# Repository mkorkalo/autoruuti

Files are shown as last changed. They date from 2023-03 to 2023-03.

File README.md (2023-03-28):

# autoruuti
Automatic gunpowder dispenser for ammunition reloading use.

Don't want to spend 1500 USD for a precision automatic powder dispenser? Build your own.
Cost for the electronics is less than 50 €, plus a laboratory scale worth about 290 €.

See [my youtube video](https://www.youtube.com/watch?v=Eo732I7xDfE&t=23s) for a short demo.

## Required hardware
These are what I used. I am not affiliated with any of these manufacturers or shops.

* [Laboratory scale KERN EMB-V 200-3V](https://vaakaekspertti.fi/laboratoratoriovaaka-kern-emb-v.html). I believe any KERN scale with RS-232 port should work, but verify that it supports the [KERN KCP protocol](https://dok.kern-sohn.com/manuals/files/English/KCP-ZB-e-v1.3.7.pdf).
* [TTL-RS232 converter](https://www.aliexpress.com/item/1005003091082827.html)
* [Arduino Uno R3 (clone)](https://www.aliexpress.com/item/1005003363526075.html)
* [LCD keypad shield (clone)](https://www.aliexpress.com/item/1005004889066625.html)
* [28BYJ-48-5V 4 phase stepper motor + ULN2003 controller board](https://www.aliexpress.com/item/1005004566735226.html)
* [Frankford Arsenal powder dispenser](https://www.metsovaruste.fi/metsastysmaailma/ruutisirotin-frankford-arsenal/p/60-025-3985/). You can use any other powder dispenser, but the included 3D model for the mechanical adapter & holder will probably not fit and adjustments will be needed.
* A 5 volt power supply directly connected to the 5V rail of the Uno board. Do not use the included 12V to 5V DC converter, it will not supply enough power for the stepper motor and you will have problems.
* A male to male RS-232 serial cable. I made my own cable from DB9 male connectors. Only TXD, RXD & GND are required (and rx/tx needs to be cross connected of course).
* A 3D printer capable of printing at least PLA. I used PETG but PLA and others should work just fine. Almost any printer will do.

## Electronic assembly

* Place LCD keypad shield on top of the arduino uno board.
* Connect 5V rail directly to the 5V rail of Uno and GND to Uno GND.
* Also connect power supply 5V & GND directly to the ULN2003 controller board.
* Connect 5V & GND to ULN2003 5V & GND.
* Connect IN1, IN2, IN3, IN4 of ULN2003 to Uno pins A5, A4, A3 and A2.
* Connect serial converter RX to D3 and TX to D2
* Recommended: USB-A male connector for supplying power to the unit. I use a USB-A male connector to power the device and I've found it works best for me. I can even power the device using a power bank.

See [Arduino UNO pinout diagram](https://images.prismic.io/circuito/8e3a980f0f964cc539b4cbbba2654bb660db6f52_arduino-uno-pinout-diagram.png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,format).

## Mechanical assembly ##

### Main case ###
* I used an [Arduino case I found from thingiverse](https://www.thingiverse.com/thing:3362327) and cut off a piece to make the display assembly fit. Print and install with screws.
* ULN2003 board can fit inside but needs an enclosure of some thing, I just used electrical tape.
* I cut off a bit to fit the TTL converter to the side.
* Better enclosure would be nice but I didn't have time to CAD model it yet. Please, share your model if you draw one.

### Powder dispenser ###
* Print cadfiles/dispenser_axle_adapter: 
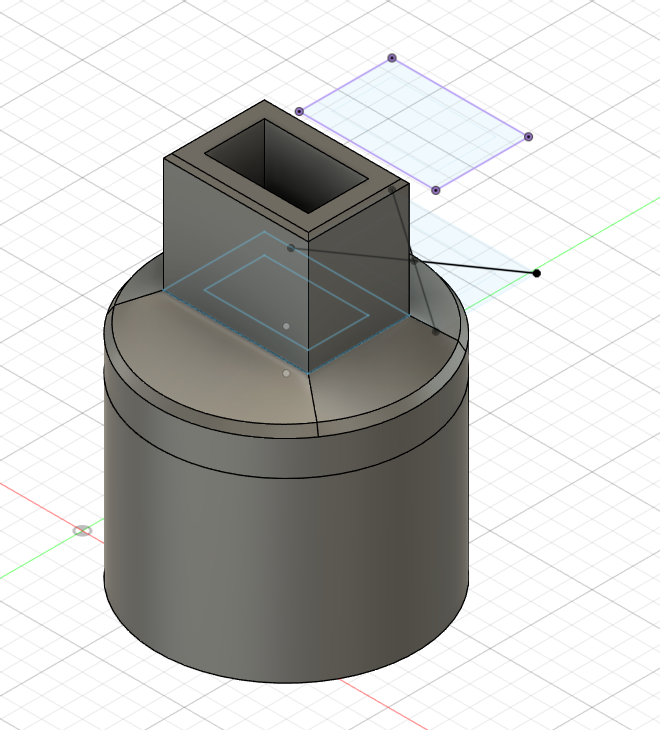
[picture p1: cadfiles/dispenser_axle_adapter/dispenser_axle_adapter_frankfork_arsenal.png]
Dispenser axle adapter


* Print cadfiles/motor_mount
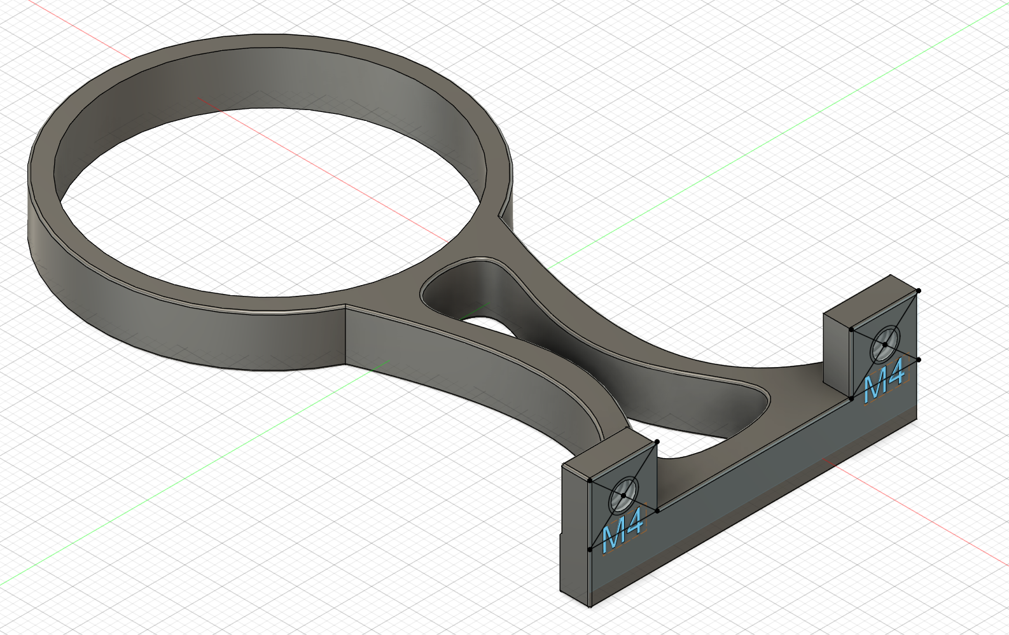
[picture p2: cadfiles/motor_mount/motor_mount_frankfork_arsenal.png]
Motor mount

* Assemble the model as seen in the youtube video. It's a tight fit but worked for me.

## Software

* Install [Arduino IDE] (https://www.arduino.cc/en/software)
* Install a few arduino libraries:
   * [Regexp by Nick Gammon](https://github.com/nickgammon/Regexp)
   * [LCDKeypad by dzindra](https://github.com/dzindra/LCDKeypad)
* Other built-in libraries used: Stepper, SoftwareSerial, EEPROM. These do not require any 3rd party downloads.

* Flash autoruuti.ino with Arduino IDE using the included USB-A - USB-B cable.
* You should see startup texts when powering the device. If not, then your display is not properly connected.

## Usage

* Menu/UI is in finnish. Contact me if you wish to use it but don't speak finnish, I can provide a translation :)
* Default values will be loaded on first boot.
* Hold the SELECT button to enter menu.
* Short press the SELECT button to enter/leave pause mode.
* Use LEFT/RIGHT keys to navigate the menu.
* Use UP/DOWN keys to change the setting: short press for a small change and long press for a large change.
* Settings are saved automatically within 5 seconds of modification. Changing the settings often will not burn out your EEPROM.
* Rightmost button is reset and will perform a hardware reset (EEPROM settings will not be lost)
* Adjust speeds to match your powder and stepper/board combination.

### Notes on accuracy of the KERN EMB-V 200

* Always ZERO your scale between cases! As the [KERN EMB-V manual](https://dok.kern-sohn.com/manuals/files/English/EMB-V-BA-e-1624.pdf) mentions, it is not accurate for dynamic add-on weighing procedures:
> Do not use balance for dynamic add-on weighing procedures, if
> small amounts of goods to be weighed are removed or added.
> The “stability compensation“ installed in the balance may result
> in displaying an incorrect measuring value!
> (Example: Slowly draining fluids from a container on the balance.)

Technically, using the scale for powder measurement is Improver use as per the definition in manual, however I have found out that the accuracy is more than enough if you don't keep adding/removing powder for a long time and zero between measurements.
You can achieve maybe about +/- 2 mg of accuracy with correct use and settings.

# License

[CC BY-NC-SA 4.0](https://creativecommons.org/licenses/by-nc-sa/4.0/)

Not for commercial use. Please contact me if you wish to sell these.
If you think some other license would work better, let me know.

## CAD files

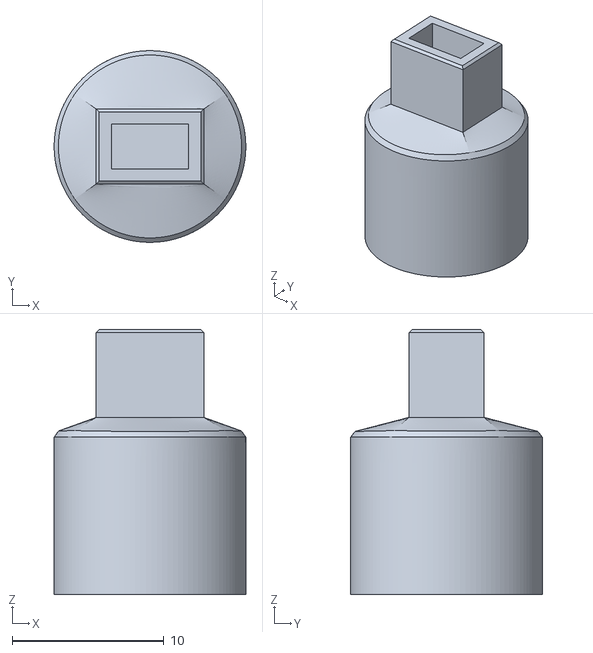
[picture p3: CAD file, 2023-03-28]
cadfiles/dispenser_axle_adapter/dispenser_axle_adapter_frankfork_arsenal.stl
12.6 x 12.6 x 17.5

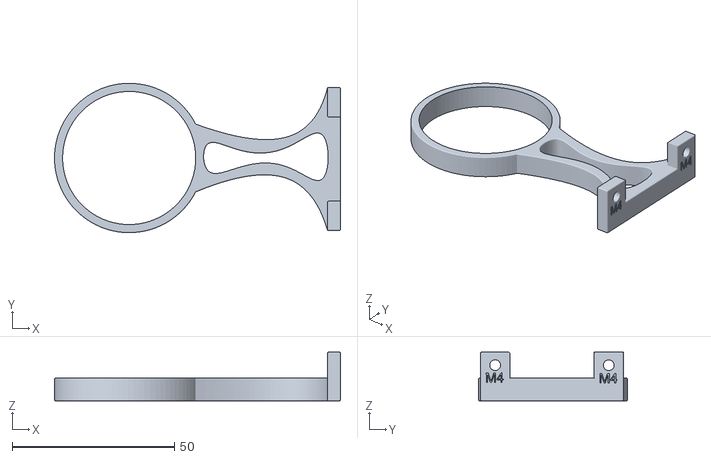
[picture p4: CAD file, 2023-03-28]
cadfiles/motor_mount/motor_mount_frankfork_arsenal.stl
88.1 x 46.0 x 15.0

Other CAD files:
cadfiles/dispenser_axle_adapter/dispenser_axle_adapter_frankfork_arsenal.f3z
cadfiles/motor_mount/motor_mount_frankfork_arsenal.f3d

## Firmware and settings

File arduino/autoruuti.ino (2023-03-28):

#include <LiquidCrystal.h>
#include <LCDKeypad.h>
#include <SoftwareSerial.h>
#include <Stepper.h>
#include <Regexp.h>
#include <EEPROM.h>

//RX: D3
//TX: D2
SoftwareSerial scale(3, 2);

LCDKeypad lcd;

int incomingByte = 0; // for incoming serial data

const int INPUT_BUFFER_SIZE = 64;
char inputBuffer[INPUT_BUFFER_SIZE];

// Defines the number of steps per rotation
const int measureTimeout = 15;

MatchState ms;

const int SCALE_ERROR_TIMEOUT = -1001;
const int SCALE_ERROR_REPLY_FORMAT = -1000;

const int LONG_BUTTON_PRESS_MS = 800;
unsigned long lastButtonDownEventMs = 0;  //in millis(). if > 0, a button down event was occured.
uint8_t lastButtonDownType;               //KEYPAD_DOWN, KEYPAD_UP etc
bool lastButtonLongPressEmitted = false;  //This is for tracking if the long press event was already emitted (so we don't do it again)
const int timerValue = 0;

const int SETTINGS_HEADER1_I = 0;
const int SETTINGS_HEADER1_V = 0xF0;
const int SETTINGS_HEADER2_I = 1;
const int SETTINGS_HEADER2_V = 0x01;
const int SETTINGS_VERSION_I = 2;
const int SETTINGS_VERSION_V = 1;
const int SETTINGS_STRUCT_I = 3;
const int STEPS_PER_ROTATION = 2038;

// Pins entered in sequence IN1-IN3-IN2-IN4 for proper step sequence
Stepper stepper(STEPS_PER_ROTATION, A5, A4, A3, A2);

uint8_t mode = 0;   //0 = operation, 1 = settings menu
#define MODE_OPERATION 0
#define MODE_SETTINGS 1

bool paused = true;
bool saveRequired = false;

#define PHASE_WAIT 0
#define PHASE_1 1
#define PHASE_2 2
#define PHASE_3 3
#define PHASE_COMPLETE 4
#define PHASE_OVERWEIGHT 5

uint8_t phase = 0;        //what phase are we in (1-3), 0=waiting startWeight, 4=complete, 5=overweight
double weight = 0.0;  //last measured weight
bool weightError = true;

#define MENUITEM_COUNT 12
uint8_t menuitem = 0;
#define MENUITEM_STARTWEIGHT 0
#define MENUITEM_TARGETWEIGHT 1
#define MENUITEM_PHASE1SPEED 2
#define MENUITEM_PHASE2SPEED 3
#define MENUITEM_PHASE3SPEED 4
#define MENUITEM_STABILIZETIMEMS 5
#define MENUITEM_PHASE1WEIGHT 6
#define MENUITEM_PHASE2WEIGHT 7
#define MENUITEM_OVERWEIGHTWARNING 8
#define MENUITEM_PHASE1ROTATIONS 9
#define MENUITEM_PHASE2ROTATIONS 10
#define MENUITEM_PHASE3ROTATIONS 11
const char *menuitem_names[] = {
  "Aloituspaino g",
  "Tavoitepaino g",
  "Vaihe 1 nopeus ask",
  "Vaihe 2 nopeus ask",
  "Vaihe 3 nopeus ask",
  "Stabilointiaika ms",
  "Vaihe 1 painoero g",
  "Vaihe 2 painoero g",
  "Ylipainovaroitus g",
  "Vaihe 1 kierrokset",
  "Vaihe 2 kierrokset",
  "Vaihe 3 kierrokset"
};
const double menuitem_modifiers_short[] = {
  0.1,
  0.001,
  1.0,
  1.0,
  1.0,
  100.0,
  0.01,
  0.002,
  0.001,
  0.05,
  0.05,
  0.05
};
const double menuitem_modifiers_long[] = {
  1.0,
  0.1,
  5.0,
  5.0,
  5.0,
  500.0,
  0.1,
  0.1,
  0.01,
  0.5,
  0.5,
  0.5
};

unsigned long settingsChangedTimeMs = 0;


// STORED SETTINGS
struct settings_t {
  double startWeight;             //e.g. 2.5    when to start addition
  double targetWeight;            //e.g. 3.3    how much we want the weight to be
  int phase1Speed; //50           //e.g. 50     phase 1 addition speed
  int phase2Speed; //20           //e.g. 20     phase 2 addition speed
  int phase3Speed; //5            //e.g. 5      phase 3 addition speed
  int stabilizeTimeMs;            //e.g. 5000   scale stabilization time in ms
  double phase1Weight;            //e.g. 0.1    when we're missing this much weight, go to phase 2
  double phase2Weight;            //e.g. 0.05   when we're missing this much weight, go to phase 3
  double overWeightWarning;       //e.g. 0.02   if we go this much over target, display a warning
  double phase1Rotations;         //e.g. 0.5
  double phase2Rotations;         //e.g. 0.25
  double phase3Rotations;         //e.g. 0.05   when doing phase 3 measurement, how much to add at once (rotations)
};

struct settings_t settings;

void loadDefaults() {
  Serial.println("load hardcoded default settings");

  //load default settings
  memset(&settings, 0, sizeof(settings_t));
  settings.startWeight = 2.0;
  settings.targetWeight = 3.3;
  settings.phase1Speed = 10;
  settings.phase2Speed = 10;
  settings.phase3Speed = 10;
  settings.stabilizeTimeMs = 5000;
  settings.phase1Weight = 0.1;
  settings.phase2Weight = 0.05;
  settings.overWeightWarning = 0.01;
  settings.phase1Rotations = 0.5;
  settings.phase2Rotations = 0.25;
  settings.phase3Rotations = 0.05;
}

void loadSettings() {
  Serial.println("load settings from EEPROM");

  //load settings from EEPROM, or if all fails, load default settings
  //#0, #1: expect static header, 0xF001
  uint8_t header1 = EEPROM.read(SETTINGS_HEADER1_I);
  uint8_t header2 = EEPROM.read(SETTINGS_HEADER2_I);
  if (header1 != SETTINGS_HEADER1_V || header2 != SETTINGS_HEADER2_V) {
    Serial.println("Header mismatch, load defaults");
    loadDefaults();
    return;
  }

  //Settings version number. Not really used right now but for future.
  uint8_t version = EEPROM.read(SETTINGS_VERSION_I);
  if (version != SETTINGS_VERSION_V) {
    Serial.println("Version mismatch, load defaults");
    loadDefaults();
    return;
  }

  //looks good, load defaults
  Serial.println("Load settings");

  EEPROM.get(SETTINGS_STRUCT_I, settings);
}

void saveSettings() {
  Serial.println("save settings to EEPROM");
  EEPROM.write(SETTINGS_HEADER1_I, SETTINGS_HEADER1_V);
  EEPROM.write(SETTINGS_HEADER2_I, SETTINGS_HEADER2_V);
  EEPROM.write(SETTINGS_VERSION_I, SETTINGS_VERSION_V);
  EEPROM.put(SETTINGS_STRUCT_I, settings);

  settingsChangedTimeMs = 0;
}

void settingsChanged() {
  settingsChangedTimeMs = millis();
}

void print_error(String error1, String error2)
{
  lcd.clear();
  lcd.setCursor(0, 0);
  lcd.print(error1);
  lcd.setCursor(0, 1);
  lcd.print(error2);
  delay(5000);
}

int readScaleMeasurement()
{
  memset(inputBuffer, 0, INPUT_BUFFER_SIZE);
  int read = scale.readBytesUntil('\n', inputBuffer, INPUT_BUFFER_SIZE - 1);
  //Serial.print("read ");
  //Serial.print(read);
  //Serial.print("\r\n");
  //for (int k=0; k<read; k++) {
  //  Serial.print(int(inputBuffer[k]));
  //}
  //Serial.print(inputBuffer);
  //Serial.print("\r\n");

  if (read == 0) {
    weightError = true;
    return SCALE_ERROR_TIMEOUT;
  }
  for (int k=0; k<read; k++) {
    if (inputBuffer[k] == '\r' || inputBuffer[k] == '\n') {
      inputBuffer[k] = 0;
    }
  }
  ms.Target(inputBuffer);
  char match = ms.Match("%s*(-*%s*%d+.%d+) g", 0);
  if (match != REGEXP_MATCHED) {
    //print_error("ERROR in reply:", inputBuffer);
    weightError = true;
    return SCALE_ERROR_REPLY_FORMAT;
  }

  //Unsafe code. GetCapture does not support max len?
  char parsedValue[50];
  ms.GetCapture(parsedValue, 0);
  String str(parsedValue);
  str.replace(" ", "");
  //Serial.print("str ");
  //Serial.print(str);
  //Serial.print("\r\n");

  double value = atof(str.c_str());
  Serial.print("Read weight: ");
  Serial.print(value, 3);
  Serial.print("\r\n");
  weight = value;
  weightError = false;
  return 0;
}

int measure(bool stable)
{
  for (int k=0; k<measureTimeout; k++) {
    //discard all data
    scale.readBytes(inputBuffer, INPUT_BUFFER_SIZE);
    lcd.setCursor(15, 1);
    lcd.print("P");

    if (stable)  {
      scale.write("S\r\n");
      //Serial.print("write S\r\n");
    } else {
      //scale does not support SI? protocol looks different from the PDF...
      scale.write("SI\r\n");
      //Serial.print("write SI\r\n");
    }
    int ret = readScaleMeasurement();
    if (ret == SCALE_ERROR_TIMEOUT) {
      delay(500);
      continue;
    } else if (ret == SCALE_ERROR_REPLY_FORMAT) {
      delay(500);
      continue;
    }
    lcd.setCursor(15, 1);
    lcd.print(" ");
    return 0;
  }
  lcd.setCursor(15, 1);
  lcd.print("E");
  return SCALE_ERROR_TIMEOUT;
}

void pause() {
  paused = true;
}

void unpause() {
  paused = false;
}

void determinePhase(bool recursive) {
  bool stableRead = true;
  if (phase == PHASE_1) {
    stableRead = false;
  }
  double beforeWeight = weight;
  int ret = measure(stableRead);
  if (ret) {
    return;
  }

  int lastPhase = phase;

  // phase 1
  if (weight > (settings.targetWeight + settings.overWeightWarning)) {
    pause();
    phase = PHASE_OVERWEIGHT;
  } else if (weight >= (settings.targetWeight - 0.001)) {
    phase = PHASE_COMPLETE;
  } else if (weight > settings.targetWeight - settings.phase2Weight) {
    phase = PHASE_3;
  } else if (weight > settings.targetWeight - settings.phase1Weight) {
    phase = PHASE_2;
  } else if (weight > settings.startWeight) {
    phase = PHASE_1;
  } else {
    phase = PHASE_WAIT;
  }

  if (!stableRead && phase != PHASE_1) {
    if (recursive) {
      //weight changed again, give up and retry later
      return;
    }
    //phase was changed from 1, run againt to do a stable reading
    determinePhase(true);
  }

  if (beforeWeight != weight || lastPhase != phase) {
    drawOperationStatus();
  }
}

void runPhase(
  ) {
  //Addition will be done only if:
  // * Measured (stabilized) weight >= minWeight and <maxWeight
  
  //Phase 1
  //- add using phase 1 speed until we measure targetWeight - phase1Weight (fast read)
  //- start phase 2
  //Phase 2
  // - add using phase 2 speed until we measure targetWeight - phase2Weight (fast read)
  // - start phase 3
  //Phase 3
  // - add using phase 3 rotations
  // - stabilize
  // - read stabilized weight
  // - if less than target, do again

  Serial.print("runPhase w=");
  Serial.print(weight, 3);
  Serial.print(" phase=");
  Serial.print(phase);
  Serial.println("");

  if (phase == 1) {
    performAddition(settings.startWeight, settings.phase1Speed, settings.targetWeight - settings.phase1Weight, settings.phase1Rotations, false, 0, settings.targetWeight + settings.overWeightWarning);
  } else if (phase == 2) {
    performAddition(settings.startWeight, settings.phase2Speed, settings.targetWeight - settings.phase2Weight, settings.phase2Rotations, false, 0, settings.targetWeight + settings.overWeightWarning);
  } else if (phase == 3) {
    performAddition(settings.startWeight, settings.phase2Speed, settings.targetWeight, settings.phase3Rotations, true, settings.stabilizeTimeMs, settings.targetWeight + settings.overWeightWarning);
  }
}

void printWeight(double weight, bool stable, double target)
{
  lcd.setCursor(0, 1);
  lcd.print(weight, 3);
  lcd.print(" / ");
  lcd.print(target, 3);
  lcd.print(" g");
  lcd.print("        ");
}

void printPhase(int phase, double phaseTarget, double finalTarget) {
  lcd.setCursor(0, 0);
  lcd.print("Target ");
  lcd.print(finalTarget);
  lcd.print(" Pha");
  lcd.print(phase);
  lcd.print("      ");
}

void performAddition(double startWeight, int speed, double target, double rotations, bool stableMeasure, int stabilizeTimeMs, double overWeightLimit) {
  if (stabilizeTimeMs) {
    delay(stabilizeTimeMs);
    while (measure(false)) {
    }
    draw();
  }
  if (weight < startWeight) {
    return;
  }
  if (weight >= target) {
    return;
  }
  lcd.setCursor(15, 1);
  lcd.print("M");
  stepper.setSpeed(speed);
  stepper.step(rotations * STEPS_PER_ROTATION);
  lcd.setCursor(15, 1);
  lcd.print(" ");
}

void setup() {
  loadSettings();

  lcd.begin(20, 2);
  lcd.clear();
  lcd.backlight();
  lcd.print("Autoruuti v1.0");

  Serial.begin(9600);
  Serial.print("booting\r\n");
  Serial.println("A");
  Serial.println(3.301 > 3.300);
  Serial.println("B");
  Serial.println(3.302 > 3.300);
  Serial.println("C");
  Serial.println(3.308 > 3.300);
  Serial.println("D");
  Serial.println(3.300 >= 3.300);
  Serial.println("E");
  Serial.println(3.301 >= 3.300);
  Serial.println("F");
  Serial.println(3.299 >= 3.300);

  scale.setTimeout(500);
  scale.begin(9600);
  lcd.setCursor(0, 1);
  lcd.print("Moottoritesti...");
  stepper.setSpeed(10);
  stepper.step(STEPS_PER_ROTATION * 0.1);
  delay(500);
  do {
    lcd.setCursor(0, 1);
    lcd.print("Puntaritesti...  ");
    while (measure(true)) {
    }
    delay(1000);
    lcd.clear();
  } while(weight <= -1000);

  //set up a timer for button checking
  noInterrupts();
  TCCR1A = 0;
  TCCR1B = 0;
  TCNT1 = timerValue;         // preload timer
  TCCR1B |= 1<<CS01;          // 8 prescaler
  TIMSK1 |= 1<<TOIE1;         // enable timer overflow interrupt ISR
  interrupts();
  determinePhase(false);
  drawOperationStatus();
}

void enterSettings() {
  mode = MODE_SETTINGS;
  drawMenu();
}

void changeSetting(bool down, bool longPress) {
  double modifier;
  if (longPress) {
    modifier = menuitem_modifiers_long[menuitem];
  } else {
    modifier = menuitem_modifiers_short[menuitem];
  }
  if (down) {
    modifier = -modifier;
  }

  switch (menuitem) {
    case MENUITEM_STARTWEIGHT:
      settings.startWeight += double(modifier);
      break;
    case MENUITEM_TARGETWEIGHT:
      settings.targetWeight += double(modifier);
      break;
    case MENUITEM_PHASE1SPEED:
      settings.phase1Speed += int(modifier);
      break;
    case MENUITEM_PHASE2SPEED:
      settings.phase2Speed += int(modifier);
      break;
    case MENUITEM_PHASE3SPEED:
      settings.phase3Speed += int(modifier);
      break;
    case MENUITEM_STABILIZETIMEMS:
      settings.stabilizeTimeMs += int(modifier);
      break;
    case MENUITEM_PHASE1WEIGHT:
      settings.phase1Weight += double(modifier);
      break;
    case MENUITEM_PHASE2WEIGHT:
      settings.phase2Weight += double(modifier);
      break;
    case MENUITEM_OVERWEIGHTWARNING:
      settings.overWeightWarning += double(modifier);
      break;
    case MENUITEM_PHASE1ROTATIONS:
      settings.phase1Rotations += double(modifier);
      break;
    case MENUITEM_PHASE2ROTATIONS:
      settings.phase2Rotations += double(modifier);
      break;
    case MENUITEM_PHASE3ROTATIONS:
      settings.phase3Rotations += double(modifier);
      break;
  }

  settingsChanged();
}

void handleSettingsButtonEvent(uint8_t button, bool longPress) {
  if (button == KEYPAD_RIGHT) {
    menuitem++;
    if (menuitem >= MENUITEM_COUNT) {
      menuitem = 0;
    }
  } else if (button == KEYPAD_LEFT) {
    if (menuitem == 0) {
      menuitem = MENUITEM_COUNT - 1;
    } else {
      menuitem--;
    }
  } else if (button == KEYPAD_UP) {
    changeSetting(false, longPress);
  } else if (button == KEYPAD_DOWN) {
    changeSetting(true, longPress);
  } else if (button == KEYPAD_SELECT) {
    if (settingsChangedTimeMs) {
      saveSettings();
    }
    mode = MODE_OPERATION;
  }
}

void buttonEvent(uint8_t button, bool longPress)
{
  Serial.print("buttonEvent: ");
  Serial.print(button);
  Serial.print(" long=");
  Serial.print(longPress);
  Serial.print("\r\n");

  if (mode == MODE_SETTINGS) {
    handleSettingsButtonEvent(button, longPress);
    draw();
    return;
  }

  if (button == KEYPAD_SELECT && !longPress) {
    if (paused) {
      unpause();
    } else {
      pause();
    }
  } else if (button == KEYPAD_SELECT && longPress) {
    enterSettings();
    settingsChanged();
  } else if (button == KEYPAD_LEFT) {
    if (longPress) {
      settings.targetWeight -= 0.5;
    } else {
      settings.targetWeight -= 0.001;
    }
    settingsChanged();
  } else if (button == KEYPAD_RIGHT) {
    if (longPress) {
      settings.targetWeight += 0.5;
    } else {
      settings.targetWeight += 0.001;
    }
    settingsChanged();
  } else if (button == KEYPAD_UP) {
    if (longPress) {
      settings.targetWeight += menuitem_modifiers_long[MENUITEM_TARGETWEIGHT];
    } else {
      settings.targetWeight += menuitem_modifiers_short[MENUITEM_TARGETWEIGHT];
    }
    settingsChanged();
  } else if (button == KEYPAD_DOWN) {
    if (longPress) {
      settings.targetWeight -= menuitem_modifiers_long[MENUITEM_TARGETWEIGHT];
    } else {
      settings.targetWeight -= menuitem_modifiers_short[MENUITEM_TARGETWEIGHT];
    }
    settingsChanged();
  }
  draw();
}

void checkButtons() {
  uint8_t button = lcd.buttonBlocking(20, 50);
  if (button == KEYPAD_BLOCKED) {
    //run again later
    return;
  }
  if (lastButtonDownEventMs) {
    //last button down event was set
    if (button == KEYPAD_NONE) {
      if (lastButtonLongPressEmitted) {
        lastButtonLongPressEmitted = false;
        lastButtonDownEventMs = 0;
        return;
      }
      //Serial.print("button was released, emit buttonEvent short press\r\n");
      buttonEvent(lastButtonDownType, false);
      lastButtonDownEventMs = 0;
      return;
    } else if (button != lastButtonDownType) {
      //Serial.print("button was changed to something else, do nothing\r\n");
      lastButtonDownEventMs = 0;
      return;
    } else if (!lastButtonLongPressEmitted) {
      //button is still being held on and no lastButtonLongPressEmitted set
      unsigned long now = millis();
      if (now - lastButtonDownEventMs > LONG_BUTTON_PRESS_MS) {
        //long button press event
        lastButtonLongPressEmitted = true;
        buttonEvent(button, true);
      } else {
        //wait until button is released or LONG_BUTTON_PRESS_MS reached
      }
    } else {
      //button is still being held on but we don't care
    }
  } else {
    if (button == KEYPAD_NONE) {
      //no down event was before and no button pressed, do nothing
    } else {
      if (lastButtonLongPressEmitted) {
        return;
      }
      //Serial.print("button down event occured\r\n");
      lastButtonDownEventMs = millis();
      lastButtonDownType = button;
    }
  }
}

ISR(TIMER1_OVF_vect)
{
  TCNT1 = timerValue;
  checkButtons();
}

void drawMenu() {
  lcd.clear();
  lcd.setCursor(0,0);
  lcd.print(menuitem_names[menuitem]);

  lcd.setCursor(0, 1);

  switch (menuitem) {
    case MENUITEM_STARTWEIGHT:
      lcd.print(settings.startWeight, 3);
      break;
    case MENUITEM_TARGETWEIGHT:
      lcd.print(settings.targetWeight, 3);
      break;
    case MENUITEM_PHASE1SPEED:
      lcd.print(settings.phase1Speed);
      break;
    case MENUITEM_PHASE2SPEED:
      lcd.print(settings.phase2Speed);
      break;
    case MENUITEM_PHASE3SPEED:
      lcd.print(settings.phase3Speed);
      break;
    case MENUITEM_STABILIZETIMEMS:
      lcd.print(settings.stabilizeTimeMs);
      break;
    case MENUITEM_PHASE1WEIGHT:
      lcd.print(settings.phase1Weight, 3);
      break;
    case MENUITEM_PHASE2WEIGHT:
      lcd.print(settings.phase2Weight, 3);
      break;
    case MENUITEM_OVERWEIGHTWARNING:
      lcd.print(settings.overWeightWarning, 3);
      break;
    case MENUITEM_PHASE1ROTATIONS:
      lcd.print(settings.phase1Rotations);
      break;
    case MENUITEM_PHASE2ROTATIONS:
      lcd.print(settings.phase2Rotations);
      break;
    case MENUITEM_PHASE3ROTATIONS:
      lcd.print(settings.phase3Rotations);
      break;
  }

}

void drawOperationStatus() {
  lcd.clear();
  lcd.setCursor(0, 0);
  if (phase == PHASE_OVERWEIGHT) {
    lcd.print("Ylipaino!");
  } else if (paused) {
    lcd.print("Tauko");
  } else if (phase == PHASE_WAIT) {
    lcd.print("Odotetaan");
  } else if (phase == 1) {
    lcd.print("Vaihe 1");
  } else if (phase == 2) {
    lcd.print("Vaihe 2");
  } else if (phase == 3) {
    lcd.print("Vaihe 3");
  } else if (phase == PHASE_COMPLETE) {
    lcd.print("Valmis");
  }

  lcd.setCursor(11, 0);
  lcd.print(settings.targetWeight, 3);

  lcd.setCursor(0, 1);
  lcd.print(weight, 3);
  if (phase == 0) {
    lcd.print(" / ");
    lcd.print(settings.startWeight, 3);
  } else if (phase == 1) {
    lcd.print(" / ");
    lcd.print(settings.targetWeight - settings.phase1Weight, 3);
  } else if (phase == 2) {
    lcd.print(" / ");
    lcd.print(settings.targetWeight - settings.phase2Weight, 3);
  } else if (phase == 3) {
    lcd.print(" / ");
    lcd.print(settings.targetWeight, 3);
  }
}

void draw() {
  if (mode == MODE_OPERATION) {
    drawOperationStatus();
  } else {
    drawMenu();
  }
}

#define SETTINGS_AUTOSAVE_DELAY_MS 5000

void loop() {
  if (settingsChangedTimeMs) {
    unsigned long now = millis();
    if (now - settingsChangedTimeMs > SETTINGS_AUTOSAVE_DELAY_MS) {
      saveSettings();
    }
  }
  if (mode == MODE_OPERATION) {
    determinePhase(false);
    if (paused) {
      return;
    }
    if (!weightError) {
      runPhase();
    }
  } else if (mode == MODE_SETTINGS) {
    //drawMenu();
    //delay(100);
  }
}
